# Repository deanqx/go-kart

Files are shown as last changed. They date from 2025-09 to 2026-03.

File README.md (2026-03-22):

# JCS-BK_1091_GO-KART_Blinker_Lenkrad_Anzeige

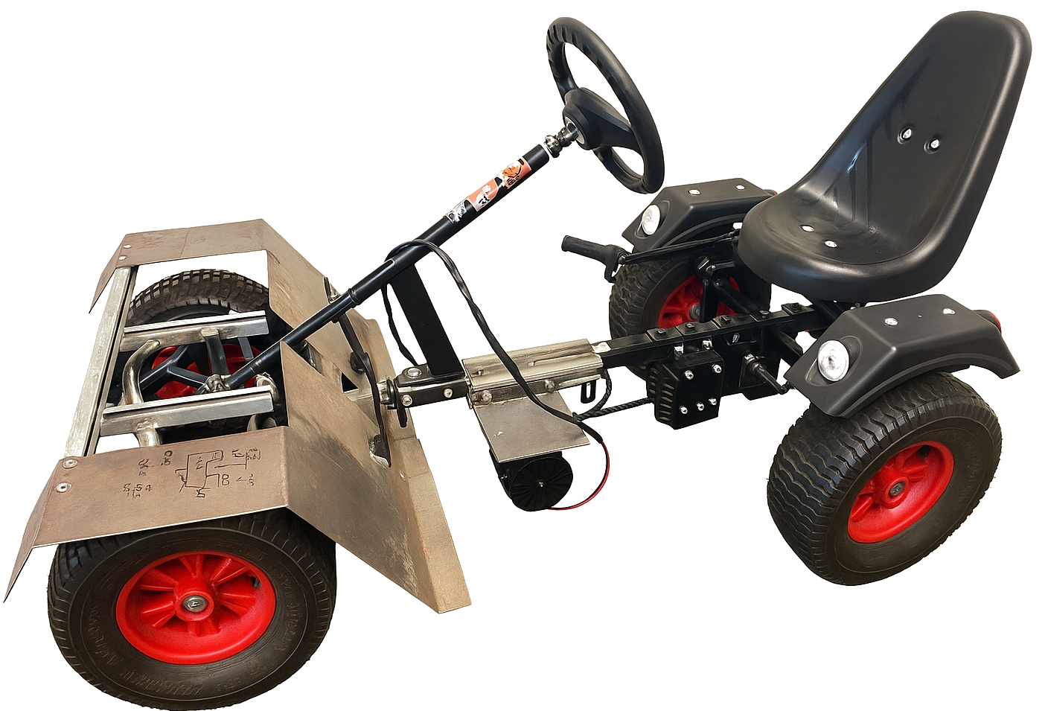
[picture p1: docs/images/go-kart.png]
Preview image of Go-Kart


Die gesamte Dokumentation befindet sich unter `docs/pdf/JCS-BK_1091_GO-KART_Blinker_Lenkrad_Anzeige_Dokumentation_DeanS.pdf` gefunden werden.

Remote repo

# Abstract

For several years, students at the technical high school have been working on upgrading a go-kart by
integrating systems typically found in modern cars. The individual modules communicate via a CAN
bus network, similar to that used in real vehicles. Two microcontrollers from the AVR family are used
throughout the system. The task is devided into multiple projects − one for each student.
This document describes the development of the light modules and the cockpit module. There is also a
video showcasing the development. The lighting system consists of four modules, one for each corner
of the vehicle. The two front modules support upper beam, lower beam, and daytime running lights,
while the two rear modules provide tail, brake, and reverse lights.
The cockpit module includes a display, a horn, and several buttons mounted on the steering wheel. It
serves as the central interface between the driver and the vehicle systems. The display presents
information such as speed, battery charge, current gear, light status, and other relevant data. Using the
steering wheel buttons and switches, the driver can control things like the driving direction, light
mode, blinker direction, horn and gear.
All required tasks of this project were successfully completed. The service provider (TIO) did not
finish the Java-based frontend; however, the serial communication interface has already been
implemented. Since the other projects have not yet integrated CAN bus communication into their
modules, communication between the cockpit and the other systems is currently not possible. In
addition, a 3D-printed case for the display and caps for the buttons could be developed in the future.

# Kurzfassung

Seit mehreren Jahren arbeiten Schüler der gymnasialen Oberstufe Bereich Technik daran, ein Go-Kart
durch die Integration von Systemen, die typischerweise in modernen Autos zu finden sind,
aufzurüsten. Die einzelnen Module kommunizieren über CAN-Bus, ähnlich wie es in echten
Fahrzeugen verwendet wird. Im gesamten System kommen zwei Mikrocontroller aus der AVR-Familie
zum Einsatz. Die Aufgabe ist in mehrere Projekte unterteilt – eines für jeden Schüler.
Dieses Dokument beschreibt die Entwicklung der Lichtanlage, des Lenkrads und der Tachoanzeige.
Des weiteren gibt es ein Video in dem die Entwicklung gezeigt wird. Die Lichtanlage besteht aus vier
Modulen, eines für jede Ecke des Fahrzeugs. Die beiden vorderen Module unterstützen Fernlicht,
Abblendlicht und Tagfahrlicht, während die beiden hinteren Module Rücklicht, Bremslicht und
Rückfahrlicht liefern.
Das Cockpitmodul umfasst ein Display, eine Hupe und mehrere am Lenkrad angebrachte Taster. Es
dient als zentrale Schnittstelle zwischen dem Fahrer und den Fahrzeugsystemen. Das Display zeigt
Informationen wie Geschwindigkeit, Batterieladestand, aktueller Gang, Lichtstatus und andere
relevante Daten an. Mit den Tasten und Schaltern am Lenkrad kann der Fahrer beispielsweise die
Fahrtrichtung, den Lichtmodus, die Blinkerrichtung, die Hupe und den Gang steuern.
Alle gegebenen Aufgaben dieses Projekts wurden erfolgreich abgeschlossen. Der Dienstleister (TIO)
hat das Java-basierte Frontend nicht fertiggestellt, jedoch wurde die serielle Schnittstelle bereits
implementiert. Da die anderen Projekte die CAN-Bus-Kommunikation noch nicht in ihre Module
integriert haben, ist eine Kommunikation zwischen dem Cockpit und den anderen Systemen derzeit
nicht möglich. Darüber hinaus könnte in Zukunft ein 3D-gedrucktes Gehäuse für das Cockpit und
Kappen für die Lenkrad-Taster entwickelt werden.

# Credits

Dieses Projekt verwendet AVR-Bibliotheken, darunter:

- Eine verbesserte Version von [dergraaf/avr-can-lib](https://github.com/dergraaf/avr-can-lib)
  welche auf den ATmega16M1 angepasst wurde.
- USART Bibliothek [jnk0le/AVR-UART-lib](https://github.com/jnk0le/AVR-UART-lib)

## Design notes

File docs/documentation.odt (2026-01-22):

BERUFLICHES GYMNASIUM
TECHNIK

JOHANN-CONRAD-SCHLAUN-BERUFSKOLLEG


Dokumentation

Go-Kart
Blinker Lenkrad Anzeige

Dean Schneider

Auftraggeber: | Michael Schmidt
Projektleitung: | Henry Otto
Projektnummer: | JCS-BK_1091_GO-KART
Jahrgang: | GYT26
Fach: | Projekt mit Elektrotechnik und Informatik
Verfasser: | Dean Schneider
E-Mail: | dschneider@schueler.jcsbk.de
Projektstart: | 1. September 2025
Projektende: | 20. März 2026
Letzte Änderung: | 22. Januar 2026

# Abstract

[englische version]

# Abstrakt

In den vergangen Jahren haben immer wieder Gruppen der gymnaliasen Oberstufe aus dem Technikbereich an dem Kettcar gearbeitet. Das Ziel ist mehrere Module eines KFZ im kleinen Aufzubauen (siehe 2.1 Team, S. 3). Dabei kommunizieren alle Module über CAN-Bus. Dies ist die Dokumentation zu dem Projekt welches die Lichtanlage, Lenkrad und die Tachoanzeige (Cockpit-Display) behandelt.

[aktueller Stand]

[was muss noch gemacht werden]

# Einleitung

Diese Dokumentation richtet sich an Personen, die dieses Projekt weiterführen oder warten möchten. Die Themen sind nach ihrer Priorität für das Nachschlagen geordnet. Das bedeutet, dass zunächst der aktuelle Aufbau (das Ergebnis) beschrieben wird, anschließend die Entwicklung hin zum aktuellen Aufbau und schließlich die Grundlagen zur Bedienung der Software.

Gesamte Anleitung für Linux um genau zu sein für die Arch Distribution.

MCU (Microcontroller Unit) entspricht Mikrocontroller

Das hier genannte Cockpit-Display wird in anderen Dokumentationen Tacho, Tachodisplay oder einfach nur Display genannt. Das OLED-Display wird Debug-Display genannt, um Verwechselung zwischen den beiden Displays zu vermeiden.

Hexadezimalzahlen werden durch 0x gekennzeichnet (z. B. 0xFF oder 0x003B).

# Ergebnis

## Team

Dieses Projekt wird in enger Zusammenarbeit mit dem Team realisiert. So muss die Kommunikation abgesprochen werden. Die Verteilung der Aufgaben sieht wie folgt aus:

Name | Aufgabe
Henry Otto | Motoransteuerung und Auslesung der Pedalen
Iuri Merklein Muniz | Elektrische Bremse und Gangschaltung
Tammo Lohe | Ladeelektronik, Batterie und Solar
Dean Schneider | Lenkrad, Cockpitdisplay und die Beleuchtung

Tabelle 1: Team

## Kommunikation zwischen den Projekten

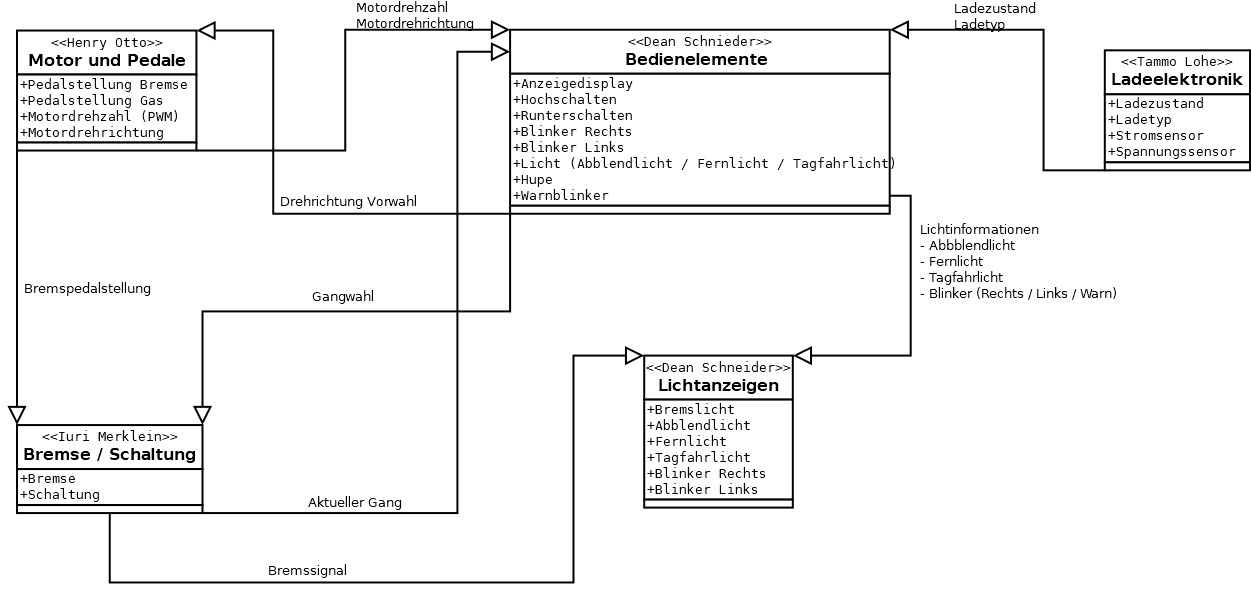
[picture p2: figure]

Abbildung 1: Kommunikationsdiagramm

## Dateistruktur

Der Quellcode und weitere Dateien des Projektes sollten von dem Projektleiter bereitgestellt werden.

├── CMakeLists.txt

├── docs

│ ├── circuit

│ │ ├── circuit.kicad_pcb

│ │ ├── circuit.kicad_prl

│ │ ├── circuit.kicad_pro

│ │ └── circuit.kicad_sch

├── libs

│ └── usart

│ ├── CMakeLists.txt

│ ├── include

│ │ ├── usart_config.h

│ │ └── usart.h

│ └── src

│ └── usart.c

├── LICENSE

├── README.md

└── src

├── cockpit_display.h

├── hal.h

└── main.c

## Mikrocontroller

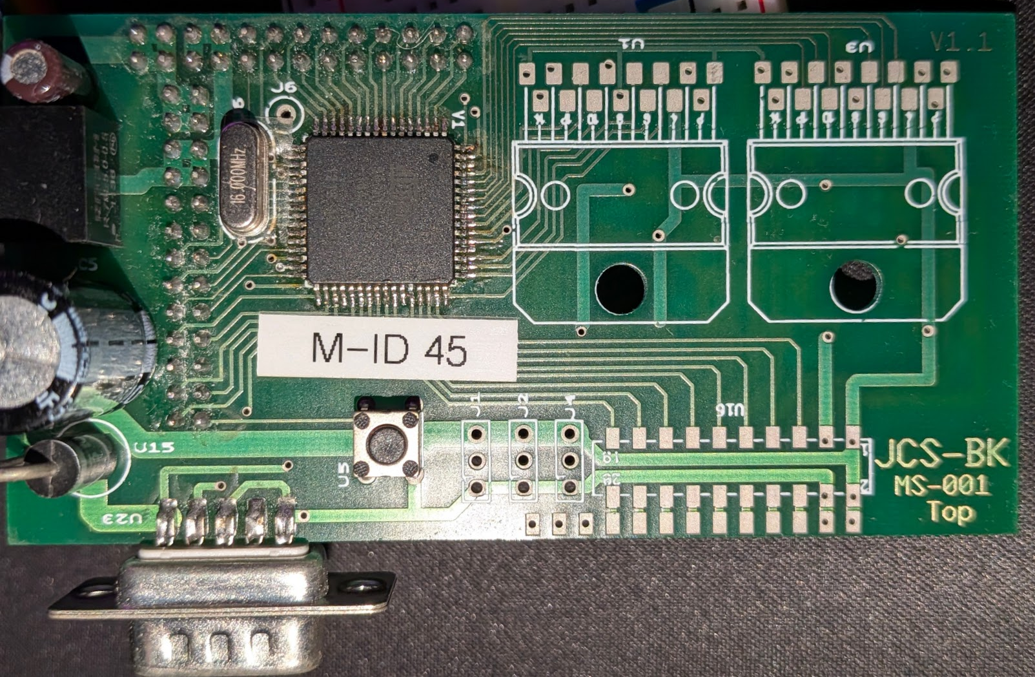
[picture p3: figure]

Abbildung 2: Masterplatine mit AT90CAN32 (MS-001)

## Cockpit-Display (Tacho)

Das Display ist von Nextion und wird mit der Nextion typischen Software programmiert/eingestellt. Auf dem Glass befindet sich ein Riss von einem Vorgänger. Christian Barth (JCS-BK_1046) hat das Display gestaltet.

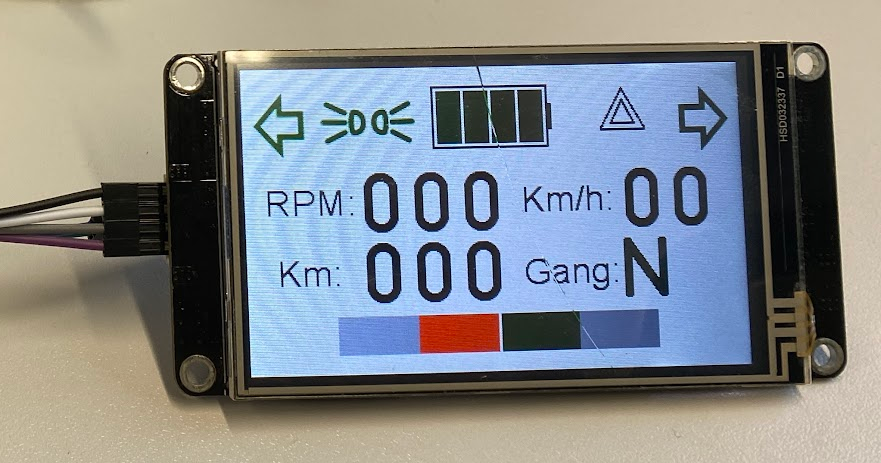
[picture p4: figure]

Abbildung 3: Cockpit-Display (NX4024K032)

[liste der befehle]

So kann man zum Beispiel mit dieser Nachricht an das Display den linken Blinker einschalten:

$ stty -F /dev/ttyUSB0 9600

$ printf 'bL.pic=1\xFF\xFF\xFF' > /dev/ttyUSB0

Erklärung dieser Befehle lässt sich unter 4.2.2 Rohdaten übertragen (siehe S. 17) finden.

## Debug-Display (OLED-Display)

Das verwendete Display ist das typische Arduino OLED-Display mit dem eingebauten SSD1306 Chip. Dieser wird über I²C angesteuert.

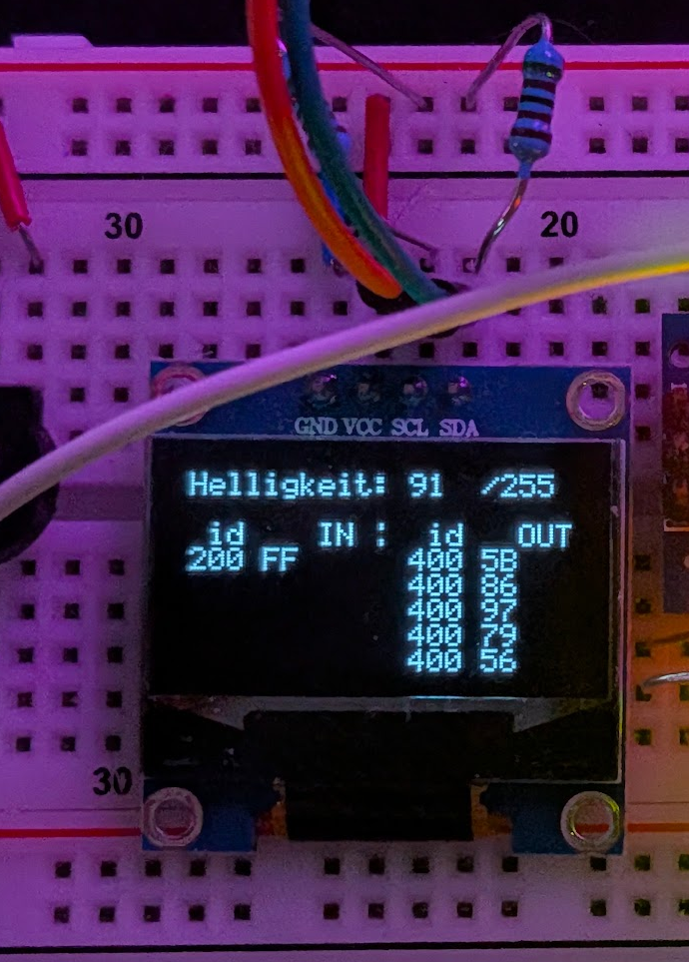
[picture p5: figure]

Abbildung 4: Debug-Display (OLED-Display mit SSD1306)

In diesem Projekt wird die Bibliothek oled-display von Sylaina (https://github.com/Sylaina/oled-display) verwendet.

## Bluetooth und UART

In diesem Projekt wird die Bibliothek AVR-UART-lib von jnk0le (https://github.com/jnk0le/AVR-UART-lib) verwendet.

Bluetooth-Name: Blinker_Anzeige

Bluetooth-Passwort: 1234

## CAN-Bus

CAN-Bus Bitrate: 125 kbits

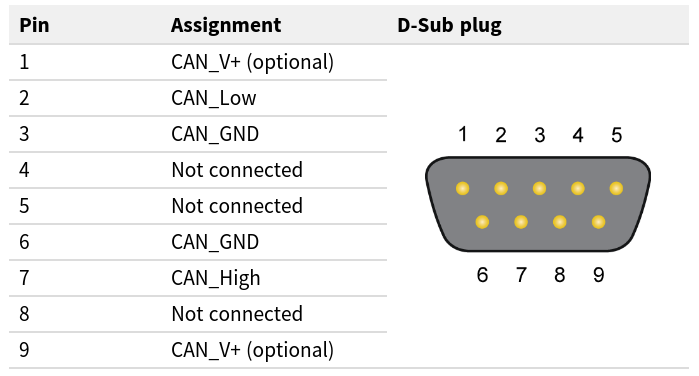
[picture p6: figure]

Abbildung 5: männlicher CAN D-Sub Anschluss nach CiA® 106 (Quelle: PCAN-USB Anleitung)

# Entwicklung

In diesem Kapitel wird der Prozess wie es Ergebnis kam dargestellt. Der aktuelle Stand des Projektes befindet sich im Kapitel 2 Ergebnis (Beginn S. 3).

## Programmierer

Ein Arduino besitzt einen Bootloader welcher den Eingang des UART in den Speicher schreibt, er programmiert sich also selbst. Allerdings besitzt der AVR MCU (AT90CAN32) von der Masterplatine keinen Bootloader, er wird über ISP (In-System Programming) programmiert.

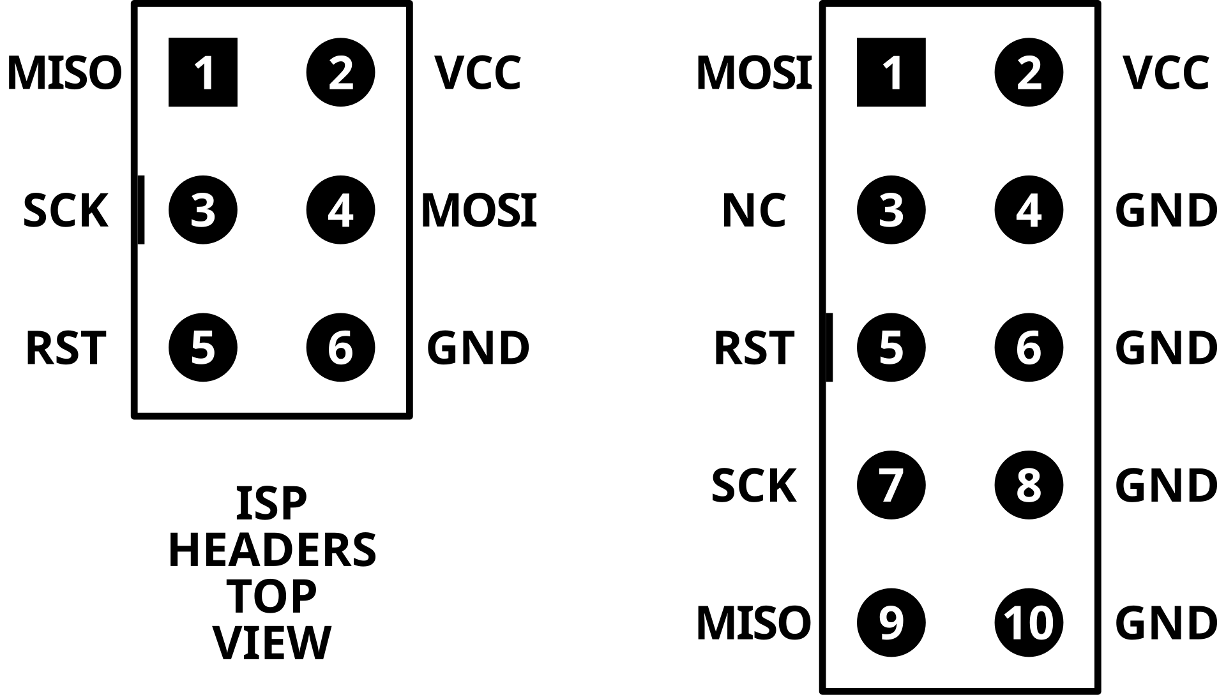
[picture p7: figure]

Abbildung 6: ISP Pinbelegung (Quelle: wikipedia.org)

Beim Kauf eines Programmierers ist darauf zu achten, dass er eine Open-Source Firmware hat, zum Beispiel USBasp.

Falls man nicht weiß welche Programmierer-Firmware man hat, kann man diese über die ID herausfinden:

$ lsusb

Zum Hochladen wird avrdude verwendet dasselbe Tool wie Microchip Studio verwendet. Als Erstes muss avrdude installiert werden. Zum Beispiel auf Arch mit:

$ sudo pacman -S avrdude

Anschließend kann man sich mit diesem Befehl alle voreingestellte Programmierer-Konfigurationen ausgeben lassen:

$ avrdude -c ?

## Masterplatine mit dem AT90CAN32

Das Projekt JCS-BK MS-001 enthält Schaltpläne zur AT90CAN32 Masterplatine. Pläne zur Addon-Platine, dass heißt dort wo die serielle und ISP Verbindung angeschlossen wird, lassen sich unter JCS-BK MS-003 finden.

### Erste Schritte

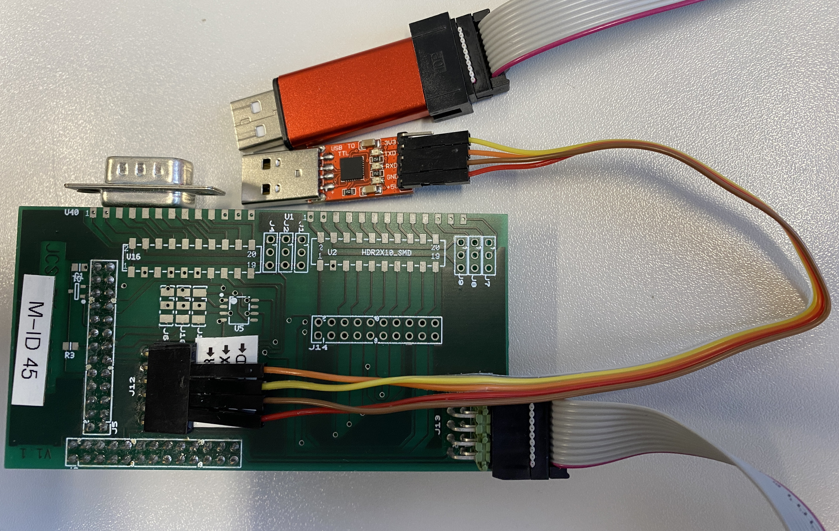
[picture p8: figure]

Abbildung 7: Masterplatine mit serieller und ISP Verbindung

Bevor man komplexe Programme programmiert sollte man erstmal die Programmier-Schnittstelle überprüfen. In diesem Beispiel wird TX zwischen High und Low gewechselt. Mein USB-zu-Seriell Gerät hat eine LED für RX, darüber kann ich den Spannungswechsel sehen. Kurz gesagt wird eine blinkende LED zum Feststellen der Funktion verwendet.

Warnung: In Abbildung 7 ist der Aufbau zu sehen. Es ist wichtig zu überprüfen ob der Programmierer eine Spannung liefert (z. B. 5V), denn dann sollte die Spannungsversorgung des USB-zu-Seriell Adapters von der Masterplatine getrennt werden. Oft ist dies nicht nötig, es reduziert jedoch das Risiko eines Schadens durch Ausgleich-Ströme.

Hier ist der Code zum Blinken lassen der RX LED (siehe 4.1 Kompilieren und Hochladen, S. 16):

#include <avr/io.h>

#include <util/delay.h>

static const uint8_t TXD1 = PD3;

int main(void) {

DDRD = 1 << TXD1;

while (1) {

PORTD ^= 1 << TXD1;

_delay_ms(500);

}

return 0;

}

## Cockpit Display (Tacho)

### Erstes Display

Eigentlich sollte das NX8048K070_011C Display von Nextion verwendet verwenden. Allerdings war ich direkt zu Beginn des Projektes unaufmerksam und habe ausversehen an das 5V Display 14V angeschlossen, das Display leuchtete bis die Spannungsversorgung entfernt wurde. Der Spannungsregler des Displays ist beschädigt und eventuell auch weitere Bauteile. Diese müssten ausgetauscht werden, wobei sich die Frage stellt ob sich der Zeitaufwand lohnt, insbesondere da es sich um SMD Bauteile handelt und man nicht eindeutig die Bauteilbezeichnung lesen kann.

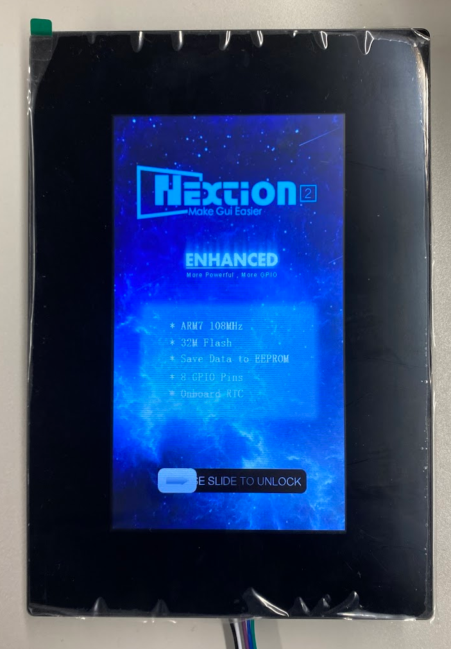
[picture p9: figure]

Abbildung 8: Nextion Display (NX8048K070_011C)

Nun muss das vorherige Display, welches allerdings von JCS-BK_1046 bereits gestaltet und eingestellt wurde, verwendet werden.

Abbildung 9: Ersatz Bauteil suche für Spannungsregler (https://smd.yooneed.one)

## Bluetooth-Modul

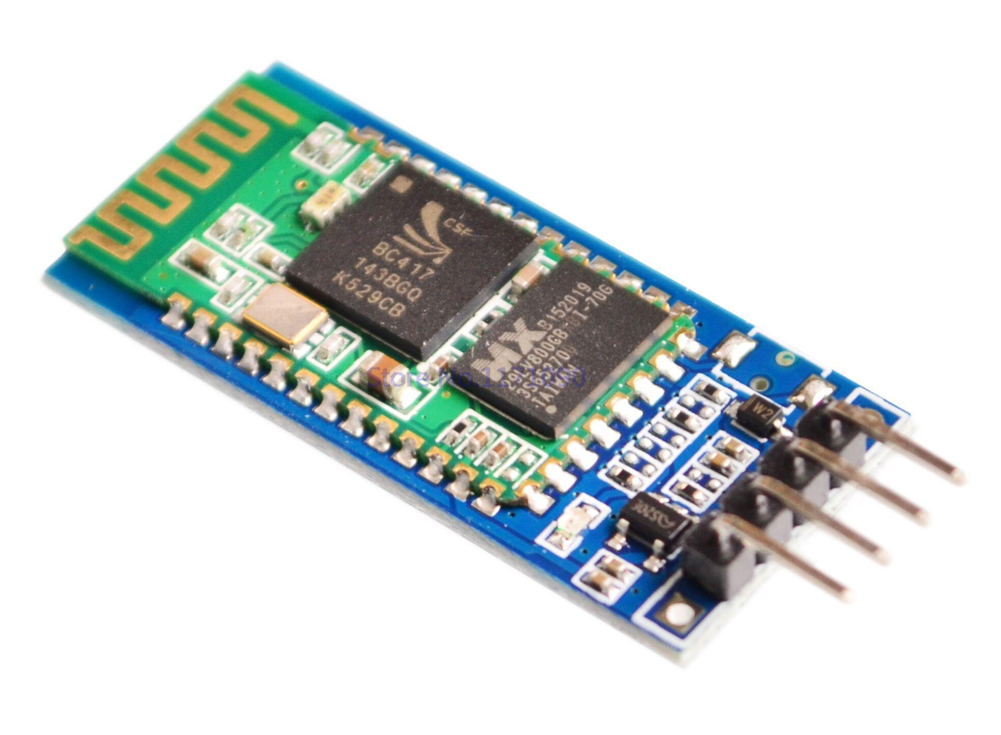
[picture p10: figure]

Abbildung 10: Bluetooth-Modul mit HC-06 Oberseite (Quelle: roboter-bausatz.de)

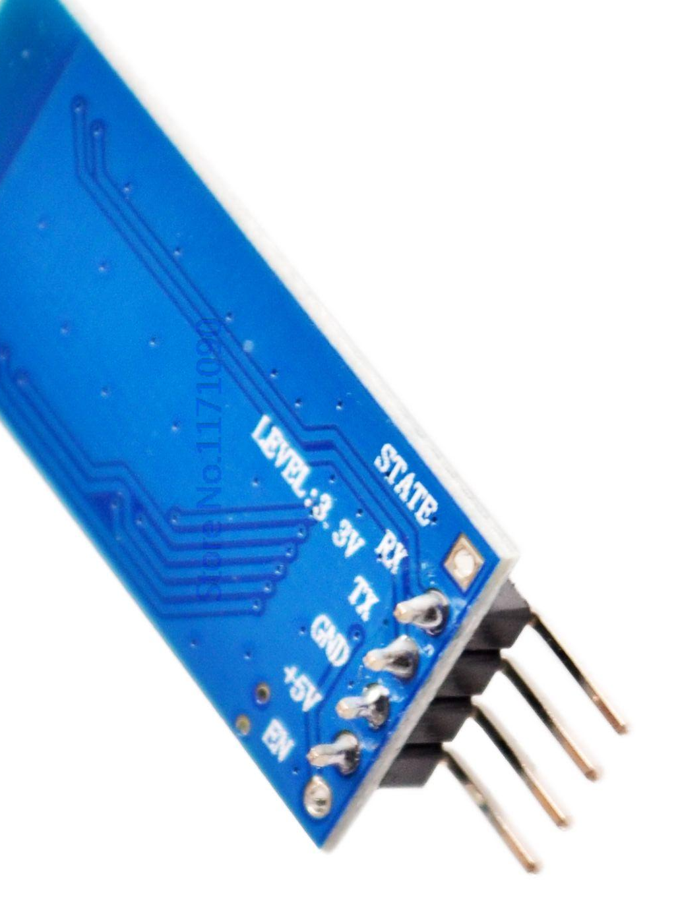
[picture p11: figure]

Abbildung 11: Bluetooth-Modul mit HC-06 Unterseite
(Quelle: roboter-bausatz.de)

In Abbildung 10 ist das verwendete Bluetooth-Modul zu sehen. Bei der grünen aufgelöteten Platine handelt es sich um den HC-06 mit dem CSR BC417BQN (Bluetooth Chip). Der HC-06 unterscheidet sich vom HC-05, indem er nur als Slave fungieren kann. Das bedeutet der HC-06 kann nicht ein Gerät (z. B. Laptop) suchen und sich mit ihm Verbinden. Zu erkennen ist der HC-06 daran, dass nur 4 Pins herausgeführt sind.

Die Pins TX und RX fungieren als UART Schnittstelle.

PIN | Beschreibung
RX (3,3V) | Receive – Eingang UART des Moduls, benötigt einen Spannungsteiler
TX | Transmit – Ausgang UART des Moduls
GND | Verbindung zu GND
5V | +5V Versorgungsspannung

### Test und konfigurieren mit USB-zu-Seriell-Konverter

Das Bluetooth-Modul wird mit dem USB-zu-Seriell-Konverter verbunden. Es sind keine Widerstände nötig da der Konverter mit 3,3 V arbeitet.

Bluetooth-Modul | USB-zu-Seriell-Konverter
RX | TX
TX | RX
GND | GND
5V | +5V

Die LED des Bluetooth-Moduls sollte blinken, sobald die Spannungsversorgung hergestellt wurde. Dies bedeutet das auf Verbindung gewartet wird.

Nun können die Befehle zum Konfigurieren über UART (siehe 4.2 UART Übertragung, S. 17) mit einer Baud-Rate von 9600 bps übertragen werden. Beim HC-06 kann kein „AT Command Mode“ aktiviert werden. Er befindet sich immer im Kommando-Modus, wenn keine Verbindung besteht was an dem Blinken der LED zu erkennen ist.

Befehl senden | Beispiel | Rückgabe vom Modul
AT | | OK
AT+VERSION | | OKlinvorV1.8
AT+NAME<Name> | AT+NAMEBlinker_Anzeige | OKsetname
AT+PIN<PIN> | AT+PIN1234 | OKsetPIN

Es gibt weitere Befehle (siehe Datenblatt). So ist es zum Beispiel möglich die BAUD-Rate zu verändern, allerdings reicht 9600 bps völlig für den UART gebrauch aus und eine Änderung kann Projekt verwirren.

Schließlich kann man sich mit einem anderen Computer über Bluetooth Verbinden und seriell Daten an den Computer mit der UART Verbindung senden (siehe 4.3 Bluetooth Übertragung, S. 19).

### Schaltung mit Mikrocontroller

Der TX Pin des Bluetooth-Moduls wird über eine Diode geleitet, da der MCU noch nicht initialisiert sein könnte und damit der RX des MCU High ist und TX Low, dadurch entsteht ein Kurzschluss. Der TX Pin des MCU wird über einen Spannungsteiler angeschlossen da der MCU mit 5V und das Modul mit 3.3 V arbeitet. Im Folgenden wird der Spannungsteiler dimensioniert.

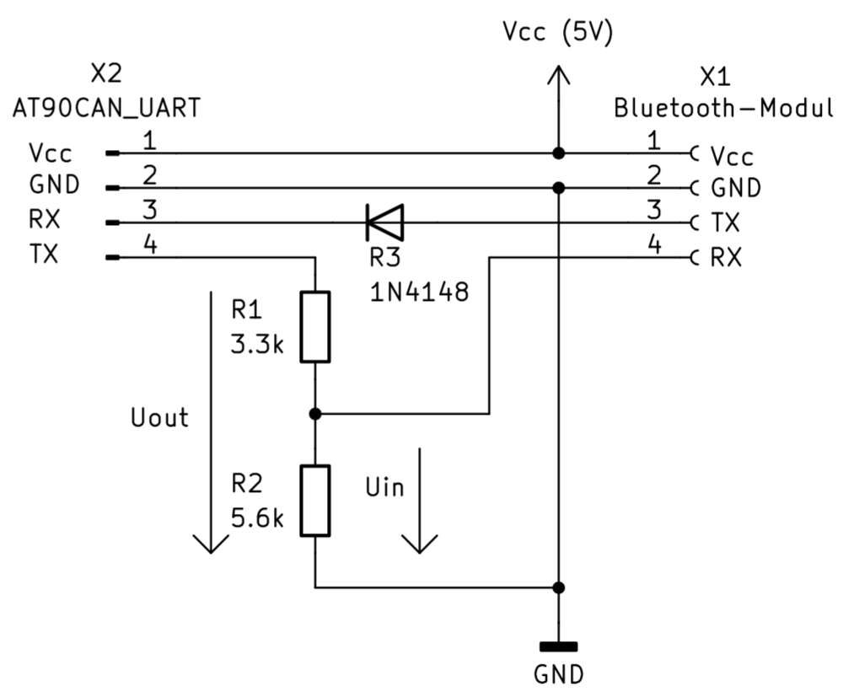
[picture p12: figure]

Schaltplanausschnitt 1: Anschluss des Bluetooth-Modul an die Masterplatine

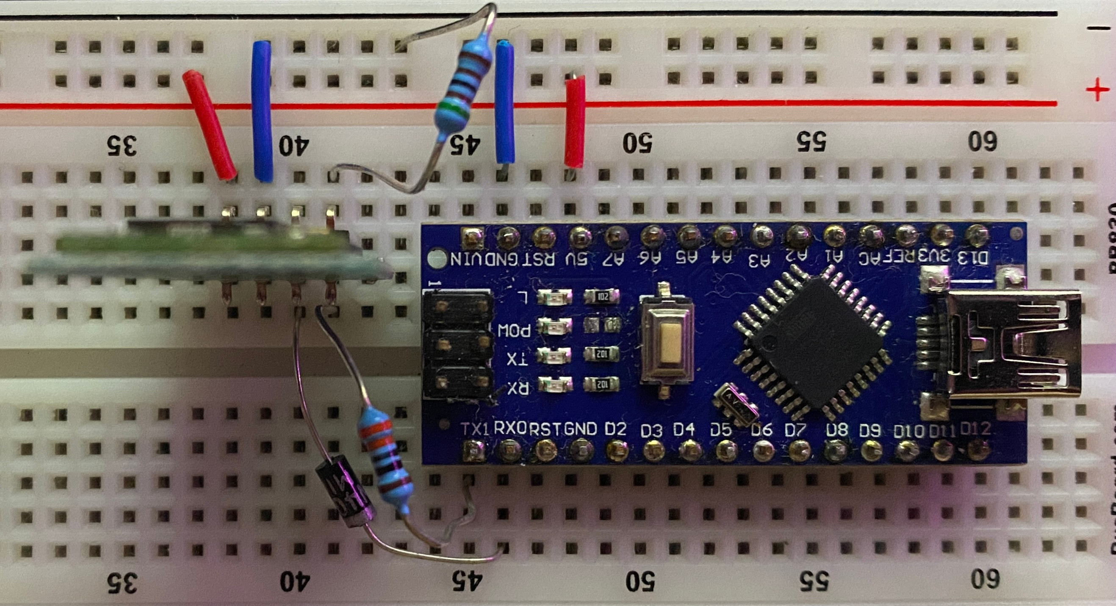
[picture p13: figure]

Abbildung 12: Bluetooth-Modul Schaltung mit Arduino

Die Eingangsspannungen beziehen sich auf den CSR BC417BQN.

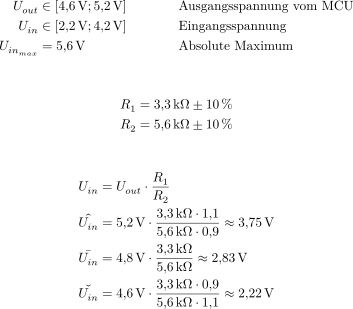
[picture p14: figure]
TexMaths 12§latex§\begin{align*} U_{out} &\in [\SI{4.6}{\volt}; \SI{5.2}{\volt}] &&\text{Ausgangsspannung vom MCU}\\ U_{in} &\in [\SI{2.2}{\volt}; \SI{4.2}{\volt}] &&\text{Eingangsspannung}\\ U_{in_{max}} &= \SI{5.6}{\volt} &&\text{Absolute Maximum} \end{align} \begin{align*} R_1 &= \SI{3.3}{\kilo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

Schließlich kann man die UART-Ausgabe über Bluetooth auslesen und Daten an den MCU über UART senden (siehe 4.3 Bluetooth Übertragung, S. 19).

Warnung: Hochladen über den Bootloader wird nicht funktionieren da ein Reset benötigt wird.

# Grundlagen

In diesem Kapitel werden die Grundlagen zur bedienung der Software erklärt. So das man dieses Projekt weiter entwickeln oder warten kann. Dabei richtet sich diese Anleitung an Linux-Nutzer, einige Programme sind ebenfalls für andere System wie Windows verfügbar.

## Kompilieren und Hochladen

Benötigtes Paket:

- cmake

CMake und Make sind Werkzeuge, die den Bau von Programmen steuern, ähnlich wie eine IDE (Microchip Studio), nur über die Kommandozeile. CMake erzeugt Baupläne, die das System und den Compiler kennen, und Make führt diese Pläne aus, übersetzt den Code und erstellt die ausführbaren Dateien.

$ cmake -B build

Dieser Befehl erzeugt in einem neuen Verzeichnis namens „build“ alle notwendigen Dateien, die für den Bau des Projekts benötigt werden. CMake liest die „CMakeLists.txt“ Datei aus dem „src“ Verzeichnis, plant welche Dateien kompiliert werden müssen, und erstellt die Bauanweisungen (Makefile).

$ make

Make liest die von CMake erzeugten Makefiles und führt die Anweisungen aus. Es kompiliert die Quellcodes in Maschinencode und erstellt daraus die fertigen Programme oder Bibliotheken. Make sorgt dafür, dass nur die geänderten Dateien neu gebaut werden, was Zeit spart.

## UART Übertragung

### Text übertragen

Benötigtes Paket:

- minicom

1. USB-zu-Seriell-Konverter Geräte Schnittstelle finden (z. B. /dev/ttyUSB0 oder /dev/ttyACM0):

$ ls /dev/tty*

2. Serielle Übertragung öffnen. In diesem Fall mit dem Tool „minicom“ und eine BAUD-Rate von 9600 bps:

$ minicom -D /dev/ttyUSB0 -b 9600

### Rohdaten übertragen

Um Binär oder Hexadezimal über UART zu senden kann man nicht minicom verwenden. In diesem Beispiel wird das Standard-Linux-Interface genutzt.

1. BAUD-Rate einstellen (z. B. 9600 bps):

$ stty -F /dev/ttyUSB0 9600

2. Nachricht senden (z. B. für das Cockpit-Display):

$ printf 'bL.pic=1\xFF\xFF\xFF' > /dev/ttyUSB0

Hierbei ist die Nachricht: „bL.pic=1“ und drei mal 0xFF.

### CAN Sniffing (PCAN-USB)

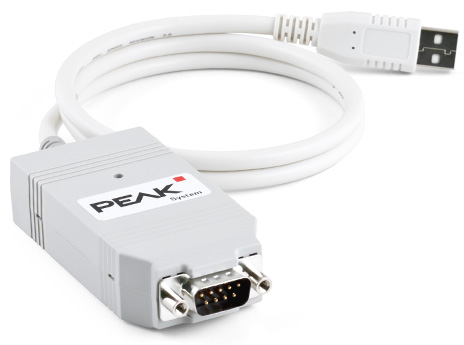
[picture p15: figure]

Abbildung 13: PCAN-USB (Quelle: peak-system.com)

Benötigte Pakete:

- can-utils

Als CAN-Interface für USB wird der PCAN-USB IPEH-002021 von PEAK-System verwendet.

Der D-Sub stecker von allen Modulen ist nach CiA® 106 (siehe Abbildung 5: männlicher CAN D-Sub Anschluss nach CiA® 106 (Quelle: PCAN-USB Anleitung), S. 8)

#### Empfangen

Der folgende Befehl aktiviert das Netzwerk-Interface can0 als CAN-Bus-Schnittstelle und setzt dabei die Übertragungsrate auf 125 kbit/s. Dieser Schritt muss nur einmal durchgeführt werden.

$ sudo ip link set can0 up type can bitrate 125000

Anschließend können Nachrichten des CAN-Busses augegeben werden.

$ candump can0

Mögliche Ausgabe:

can0 400 [8] 01 02 02 03 04 05 06 07

#### Senden

Beispiel mit ID = 0x4AA und erstes Datenbyte = 0x0F, zweites Datenbyte = 0x55:

$ cansend 4AA#0F55

#### Fehlerbehebung

Eventuell muss der Treiber von PEAK-System manuell installiert werden.

Ob ein Treiber installiert ist kann man zum Beispiel über die System-Logs herausfinden. Da der Treiber jenach Distrobution auch anders als peak_usb benannt sein kann, muss man eventuell den gesuchten Eintrag mit can0, pcan oder peak suchen.

$ sudo dmesg | grep -i peak_usb

Wenn die Ausgabe so ähnlich aussieht ist der Treiber installiert:

peak_usb 3-2:1.0: PEAK-System PCAN-USB adapter hwrev 28 serial

peak_usb 3-2:1.0 can0: attached to PCAN-USB channel 0

usbcore: registered new interface driver peak_usb

Falls der Treiber nicht installiert ist kann man ihn über den Package-Manager des Systems herunterladen oder über die Webseite von PEAK-Systems.

## Bluetooth Übertragung

In diesem Kapitel wird erklärt wie man eine Verbindung mit dem Bluetooth-Modul (siehe 3.4 Bluetooth-Modul, S. 12) aufnehmen kann.

Warnung: IOS unterstützt keine Verbindung zu SPP (Serial Port Profile), sondern nur BLE (Bluetooth Low Energy). Da es sich hier um SPP handelt, ist keine Verbindung mit dem iPhone oder iPad möglich.

Benötigte Pakete:

- minicom
- bluez
- bluez-deprecated-tools

Die Arch Wiki hat eine ausführliche Erklärung wie man sich mit einem Bluetooth-Gerät verbindet (siehe https://wiki.archlinux.org/title/Bluetooth).

Nachdem eine Bluetooth-Verbindung hergestellt wurde, muss sie einer device-Datei gebunden werden:

$ sudo rfcomm bind rfcomm0 <MAC Addresse des Bluetooth-Moduls>

Anschließend kann eine serielle Übertragung (siehe 4.2 UART Übertragung, S. 17) mit einer BAUD-Rate von 9600 bps hergestellt werden:

$ minicom -D /dev/rfcomm0 -b 9600

Das Blinken auf dem Bluetooth-Modul sollte aufhören und die Status-LED sollte konstant Leuchten.

# Eidesstattliche Erklärung

Hiermit versichere ich, dass ich die vorliegende Dokumentation selbstständig verfasst und keine anderen als die angegebenen Quellen und Hilfsmittel benutzt habe. Alle Stellen, die wörtlich oder sinngemäß aus veröffentlichten oder nicht veröffentlichten Schriften entnommen wurden, sind als solche kenntlich gemacht.

Ferner versichere ich, dass die vorliegende Arbeit noch nicht in einem anderen Prüfungsverfahren vorgelegen hat.

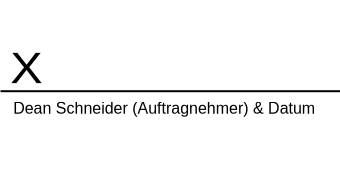
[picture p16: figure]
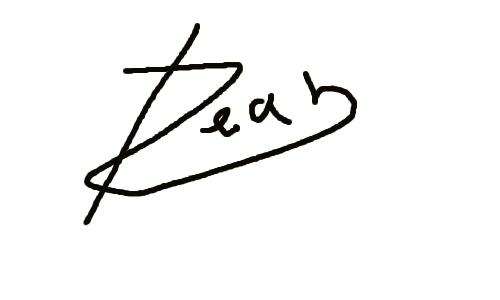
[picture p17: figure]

# Anhang

## Projekte der Vorgänger

Hiervon sind hauptsächlich JCS-BK_1025 (Schaltpläne für Lichtanlage), JCS-BK_1049 (Lichtanlage) und JCS-BK_1046 (Lenkradknöpfe, Cockpitdisplay) von Bedeutung.

Tabelle 2: alte Projekte

## Tagesziele

Tabelle 3: Tagesziele

## Meilensteine

Start- datum | Ziel- datum | Zeit(h) | Thema (Aufgabe)
01.09.25 | 11.09.25 | | Festlegen des Themas und der Projektteams (Informationssammlung, Pflichtenheft zur Aufgabenfixierung, Aufgabenverteilung im Team und Anfertigung des Detailterminplans)
12.09.25 | 08.10.25 | 18 | Abgabe des Pflichtenhefts
08.10.25 | 30.11.25 | 34 | Schaltplanerstellung / Programmierung von Modulen / Testaufbau / Modultests
08.10.25 | 30.11.25 | 5 | Abgabe der Draft 1 - Dokumentationsentwurf
| | | Statusermittlung / Terminplanprüfung
| | | Schaltplan- und Layouterstellung / Programmierung von Modulen Testaufbau / Modultests / Dokumentation
| | | Programmtests, Dokumentation, Fehleranalyse, Fehlerbeseitigung
| | | Abgabe der Draft2-Dokumentation 7:35 keine Verlängerung
| | | Programmtests, Dokumentation, Fehleranalyse, Fehlerbeseitigung
| | | Präsentation des Projekts Weiterentwicklung
| | | Präsentation der Ergebnisse als Impress-Vortrag
| | | Präsentation der Zwischenstände am Tag der offenen Tür
| | | Abgabe des Projekts mit Abschluss-Dokumentation 24:00
| | | Leistungsüberprüfung / Produktabnahme

## Terminplan

Tabelle 4: Terminplan 01.09. - 19.09.2025

Tabelle 5: Terminplan 20.10. - 07.12.2025

Tabelle 6: Terminplan 08.12.2025 - 25.01.2026

Tabelle 7: Terminplan 26.01. - 15.03.2026

Tabelle 8: Terminplan 16.03. - 10.05.2026

## Abbildungsverzeichnis

Abbildung 1: Kommunikationsdiagramm 3

Abbildung 2: männlicher CAN D-Sub Anschluss nach CiA® 106 (Quelle: PCAN-USB Anleitung) 5

Abbildung 3: ISP Pinbelegung (Quelle: wikipedia.org) 6

Abbildung 4: Masterplatine mit serieller und ISP Verbindung 7

Abbildung 5: (https://smd.yooneed.one) 8

Abbildung 6: Bluetooth-Modul mit HC-06 Oberseite (Quelle: roboter-bausatz.de) 9

Abbildung 7: Bluetooth-Modul mit HC-06 Unterseite (Quelle: roboter-bausatz.de) 9

Abbildung 8: Bluetooth-Modul Schaltung mit Arduino 11

Abbildung 9: PCAN-USB (Quelle: peak-system.com) 14

## Schaltplanausschnitte

Schaltplanausschnitt 1: Anschluss des Bluetooth-Modul an die Masterplatine 11

## Tabellenverzeichnis

Tabelle 1: Team 3

Tabelle 2: alte Projekte 17

Tabelle 3: Tagesziele 18

Tabelle 4: Terminplan 01.09. - 19.09.2025 20

Tabelle 5: Terminplan 20.10. - 07.12.2025 21

Tabelle 6: Terminplan 08.12.2025 - 25.01.2026 22

Tabelle 7: Terminplan 26.01. - 15.03.2026 23

Tabelle 8: Terminplan 16.03. - 10.05.2026 24

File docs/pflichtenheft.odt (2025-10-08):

BERUFLICHES GYMNASIUM
TECHNIK

JOHANN-CONRAD-SCHLAUN-BERUFSKOLLEG


Pflichtenheft

Go-Kart
Blinker Lenkrad Anzeige

Dean Schneider

Auftraggeber: | Michael Schmidt
Projektleitung: | Henry Otto
Projektnummer: | JCS-BK_1091_GO-KART
Jahrgang: | GYT26
Fach: | Projekt mit Elektrotechnik und Informatik
Verfasser: | Dean Schneider
E-Mail: | dschneider@schueler.jcsbk.de
Projektstart: | 1. September 2025
Projektende: | 20. März 2026
Letzte Änderung: | 8. Oktober 2025

# Einleitung

Dieses Dokument beschreibt wie die im Lastenheft festgelegten Anforderungen umgesetzt werden.

## Team

Dieses Projekt wird in enger Zusammenarbeit mit dem Team realisiert. So muss die Kommunikation abgesprochen werden. Die Verteilung der Aufgaben sieht wie folgt aus:

Name | Aufgabe
Henry Otto | Motoransteuerung und Auslesung der Pedalen
Iuri Merklein Muniz | Elektrische Bremse und Gangschaltung
Tammo Lohe | Ladeelektronik, Batterie und Solar
Dean Schneider | Lenkrad, Cockpitdisplay und die Beleuchtung

Tabelle 1: Team

## Kommunikation zwischen den Projekten

# Aufgabenstellung


Abbildung 1: Kommunikationsdiagramm

Entwicklung und Realisierung eines fahrzeuggestützten Armaturenbretts (Cockpitdisplay) auf Basis eines Mikrocontrollers mit Anzeige- und Bedienelementen, CAN-Bus-Anbindung, Test-Schnittstellen (Bluetooth/USB) und begleitender Dokumentation. Die Auswertungssoftware liefert die TIO.

## Hardwareanforderungen

Die folgende Aufzählung enthält Produkte von vorherigen Projekten. Falls diese nicht mehr vorhanden oder funktional sind, müssen diese dementsprechend ersetzt werden. Gegebenenfalls müssen Bauteile bestellt werden.

### Steuerung mit Mikrocontroller

Jedes Element des Go-Karts (z. B. Blinker oder Cockpitdisplay) besitzt einen eigenen Mikrocontroller. Die Mikrocontroller sind über einen CAN-Bus verbunden. Zum Einsatz kommt der ATmega16M1, der über einen integrierten CAN-Controller sowie eine UART-Schnittstelle verfügt. Voraussichtlich werden zwei UART-Schnittstellen benötigt. Die zweite Schnittstelle wird dabei softwareseitig über eine Bibliothek realisiert. Die Leiterplatte, auf der der ATmega16M1 montiert ist, wird als Masterplatine bezeichnet.

Eventuell wird der ATmega16M1 durch den stärkeren AT90CAN32 Mikrocontroller ausgetauscht. Die wichtigsten Vorteile für dieses Projekt sind unter anderem:

- zwei USART-Schnittstellen gegenüber einer beim ATmega16M1
- stärkerer CAN-Controller mit mehr Funktionen und Message Objects:
  - AT90CAN32: 15 Full Message Objects
  - ATmega16M1: 6 Message Objects
- Hardware I²C-Controller

### Beleuchtung

Front- und Rückleuchten wurden im Vorgängerprojekt erstellt (siehe 3.1.3 JCS-BK_1071_GO-KART Blinker_Lenkrad_Anzeige, S. 8).

### Lenkrad mit Steuerknöpfen

Folgende Bedienelemente sind am Lenkrad vorgesehen:

- Hochschalten
- Blinker links
- Licht (Aus / Tagfahrlicht / Fernlicht)
- Hupe
- Blinker rechts
- Herunterschalten

### Cockpitdisplay

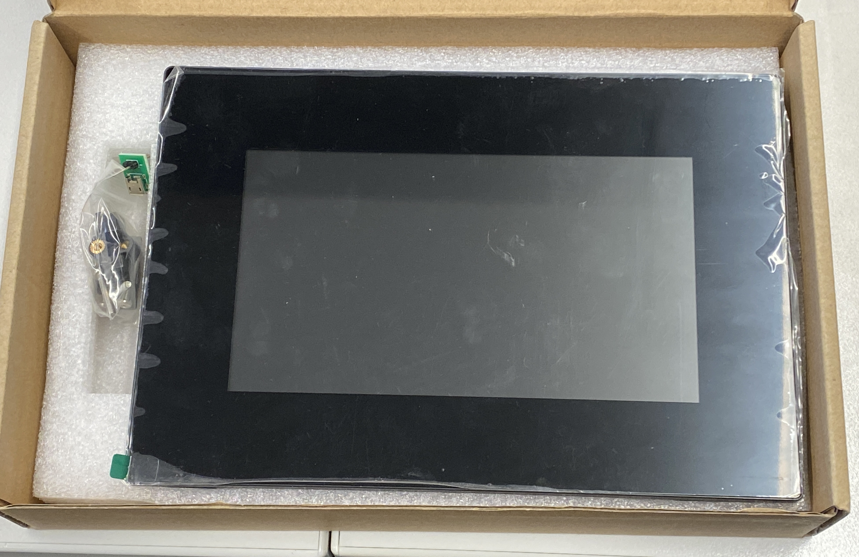
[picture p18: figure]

Abbildung 2: Display (Nextion NX8048K070)

In Abbildung 2 sieht man das Display, welches auf dem Fahrzeugarmaturenbrett befestigt wird. Das eingesetzte Display inklusive Gehäuse wird als Cockpitdisplay bezeichnet.

Das Display muss mindestens folgende Statusanzeigen darstellen: Geschwindigkeit, Batteriestatus, Gangstellung, Blinkerstatus, Fernlicht, Tagfahrlicht, Bremslicht

## Datenaustausch

### Primäre Busschnittstelle

CAN-Bus wird zum Austausch von Sensordaten und Steuerbefehlen für Systeme innerhalb des Fahrzeugs verwendet.

### Auswertungsprogramm

Ein Auswertungsprogramm, basierend auf Java, wird von der TIO erstellt. Aufbau der grafischen Benutzeroberfläche und die projektspezifische Schnittstelle sind in Abstimmung mit der TIO und dem Auftraggeber festzulegen.

### Diagnoseschnittstellen

Für jede Masterplatine stehen Bluetooth- und USB-Schnittstellen zur Verfügung. Diese ermöglichen die Kommunikation zwischen einer Masterplatine und einem Computer, auf dem die Auswertungssoftware ausgeführt wird. Die Kommunikation zwischen den Masterplatinen erfolgt ausschließlich über den CAN-Bus.

## Programmierung

Folgende Spezifikationen betreffen nur die Mikrocontroller-Programmierung und nicht das Auswertungsprogramm. Als Programmiersprache wird C eingesetzt. Programmablaufpläne werden für eine Gesamtübersicht des Programms erstellt, sie stellen den gesamten Programmablauf dar und nicht unbedingt die interne Logik. Vom Quellcode und von der Dokumentation werden regelmäßig Backups angefertigt.

### Build-Tool

Als Build-Tool wird CMake verwendet. Es wird zum Kompilieren und Hochladen der C-Dateien verwendet. Es übernimmt den Job von Atmel/Microchip Studio und ist dabei nicht an eine IDE gebunden. Außerdem ist CMake für alle Betriebssysteme (Windows, Mac und Linux) verfügbar. Alle nötigen Einstellungen können in einfachen Textdateien (CMakeLists.txt) festgelegt werden. Für AVR-Projekte nutzt man dann die Toolchain avr-gcc sowie Tools wie avr-objcopy und avrdude zum Hochladen über die serielle Schnittstelle.

Für dieses Programm wird eine genauere Erklärung erstellt.

### Code Konventionen

- Einheitliche Einrückung mit 4 Leerzeichen (keine Tabs)
- Maximale Zeilenlänge von 80 Zeichen
- Variablen und Funktionen: snake_case
- Konstanten: UPPER_CASE
- Aussagekräftige Namen statt Abkürzungen (calculate_total statt calc)
- Kommentare richten sich nach dem Google Style C++ Guide (https://google.github.io/styleguide/cppguifde.html#Comments)

## Dokumentation

### Office-Software

Als Office-Software wird LibreOffice verwendet. LibreOffice ist ein kostenloses und leistungsfähiges Office-Paket, das eine Vielzahl von Programmen für unterschiedliche Anwendungsbereiche bietet. Calc ist das Tabellenkalkulationsprogramm, mit dem man Daten berechnen, auswerten und in Diagrammen darstellen kann. Writer ist das Textverarbeitungsprogramm, das sich für das Schreiben und Formatieren von Dokumenten wie Briefe, Berichte oder wissenschaftliche Arbeiten eignet. Draw ist das Grafik- und Zeichenprogramm, mit dem man Diagramme, Skizzen, Flusspläne oder auch komplexe Illustrationen erstellen kann.

### Projekt-Dokumentation

Die Projekt-Dokumentation hält sich an die Stilvorgaben (definiert unter „Inhalt und Aufbau der Dokumenation“ im Lastenheft). Die Projekt-Dokumenation wird in LibreOffice Writer geschrieben und wird als PDF exportiert. Sie richtet sich an jemanden, welcher nichts über das Go-Kart weiß. Es wird vorausgesetzt das der Leser alles aus der Unter- und Mittelstufe des Technischen Gymnasium weiß. Die Dokumentation beinhaltet alle Informationen, um diese Aufgabenstellung fortzuführen.

### Plakat für den Tag der offenen Tür

Das Plakat stellt dieses Projekt visuell dar.

### Projektvideo

Wichte Ereignisse werden auf Video festgehalten und am Ende wird ein Zusammenschnitt erstellt, welche das Projekt visuell dokumentieren.

### Abschlusspräsentation

Zum Schluss wird eine Präsentation mit LibreOffice Impress erstellt, welche das Projekt in 15 bis 20 Minuten zusammen fasst.

## 3D-Druck

Eventuell müssen für das Display und das Lenkrad Teile aus Plastik mit dem 3D-Drucker der Schule gedruckt werden. Als CAD-Software wird FreeCAD verwendet.

## Erstellung von Platinen

Eventuell müssen Platinen gefertigt werden. Die Platinenlayouts werden mit KiCad erstellt und in das benötigte Format exportiert. Die Leiterbahnen werden nach den Vorgaben des Fräsers erstellt.

KiCad ist ein kostenloses und plattformübergreifendes EDA-Programm, das wie Multisim für das Entwerfen von Schaltplänen und Leiterplatten verwendet wird. Im Gegensatz zu Multisim ist es vollständig Open Source, läuft stabil unter Linux und wird kontinuierlich weiterentwickelt. Viele Nutzer bevorzugen KiCad, weil es weniger Fehler aufweist, professionell nutzbar ist und keine Lizenzkosten verursacht.

# Projekte der Vorgänger

Tabelle 2: alte Projekte

## Analyse des Bestehenden

Es ist davon auszugehen das die Bauteile aus den Vorgängerprojekten nicht funktionsfähig sind. Sie müssen dementsprechend ersetzt werden.

### JCS-BK_1046_GO-KART Fahrzeugarmaturenbrett

Aus der Dokumenation geht nicht hervor welche Funktion diese Bauteile erfüllen. Da der Auftrag dieses Projektes das Fahrzeugarmaturenbrett ist, kann man davon ausgehen das, das die Taster zum Steuern der Beleuchtung genutzt wird. Wie brauchbar diese Bauteile sind muss nochmal genauer untersucht werden.

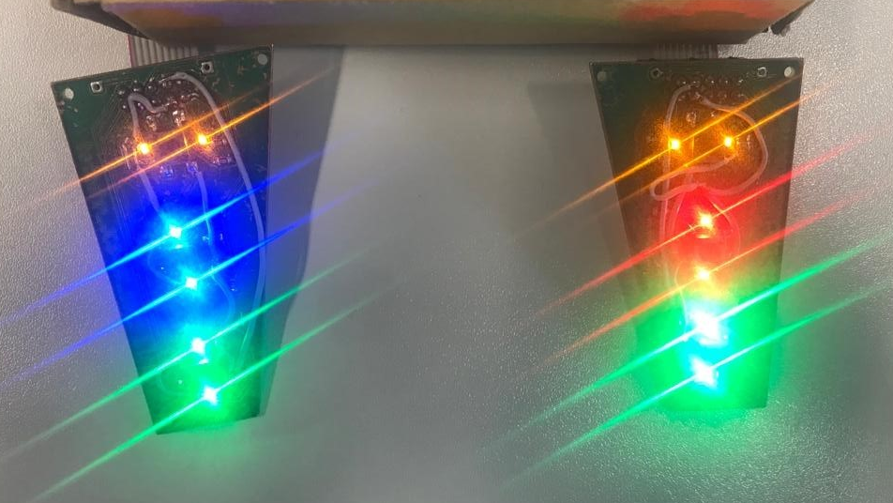
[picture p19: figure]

Abbildung 5: Tasterplatinen (JCS-BK_1046)

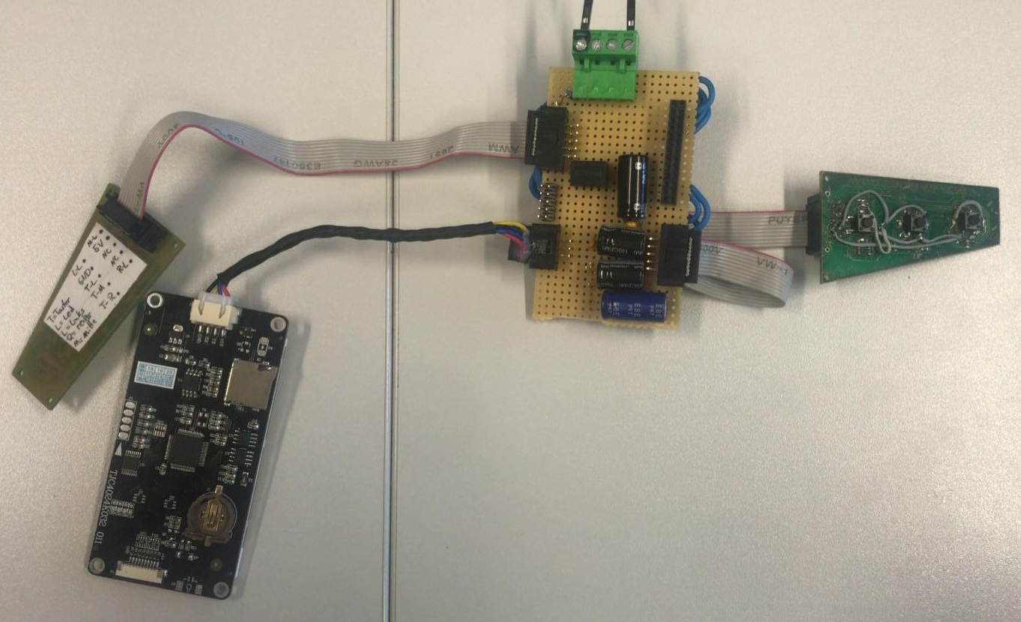
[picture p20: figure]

Abbildung 3: Adapterplatine verbunden mit Tasterplatine (JCS-BK_1046)

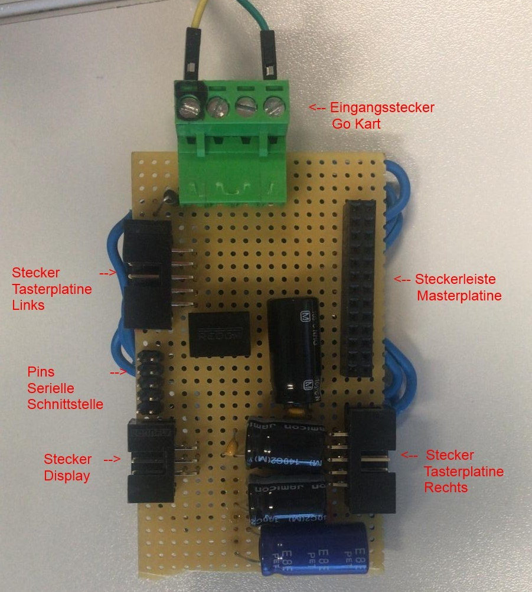
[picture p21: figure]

Abbildung 4: Adapterplatine (JCS-BK_1046)

### JCS-BK_1049_GO-KART Lichtanlage

Die Lichtanlage wurde von dem letzten Projekt (JCS-BK_1071) überarbeitet.

### JCS-BK_1071_GO-KART Blinker_Lenkrad_Anzeige

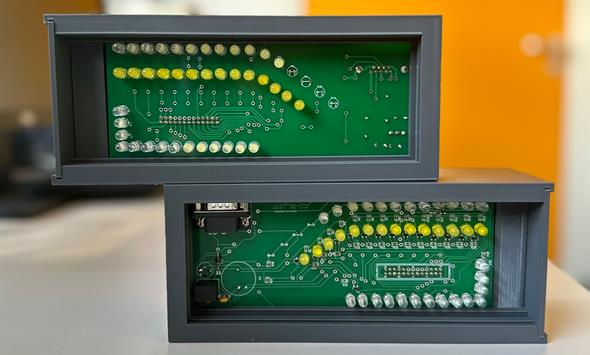
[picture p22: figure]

Abbildung 6: Frontlicht (JCS-BK_1071)

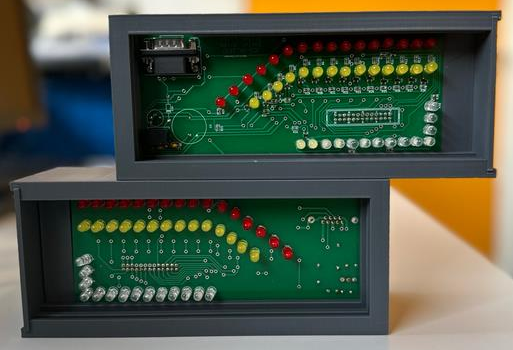
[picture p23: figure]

Abbildung 7: Rücklicht (JCS-BK_1071)

In Abbildung 8 sieht man die Masterplatine, welche in jedem Element eingebaut ist:

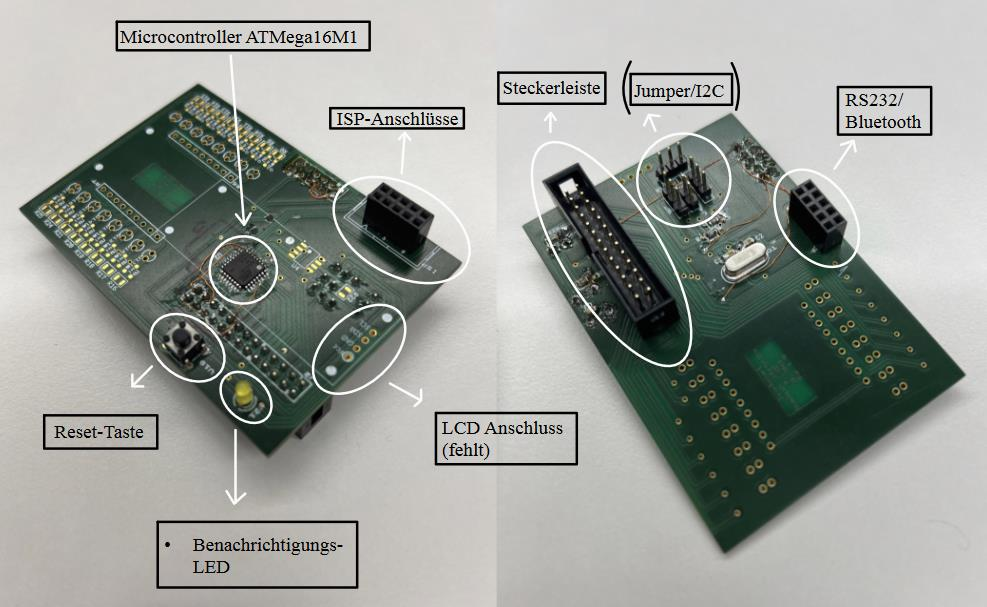
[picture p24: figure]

Abbildung 8: Masterplatine (JCS-BK_1071)

- Cockpit
- Frontlicht rechts und links
- Rücklicht rechts und links

Aus der Dokumentation des Vorgängers lässt sich schließen das die Front- und Rücklicht funktionsfähig sind.

Sofern ein Austausch durch den AT90CAN32 vorgenommen werden soll, kann die aktuelle Masterplatine nicht weiterverwendet werden. Da der AT90CAN32 über 64 Pins verfügt, während der bisher eingesetzte ATmega16M1 nur 32 Pins besitzt, ist die Anfertigung einer neuen Masterplatine erforderlich. Zudem ist der AT90CAN32 ausschließlich in einem SMD-Gehäuse erhältlich, wodurch die Verwendung eines Breadboards für den Prototypen ausgeschlossen ist.

# Ablauforganisation

Da die Zeit sehr knapp ist und das Cockpitdisplay von den anderen Projekten des Teams abhängig ist, muss man davon ausgehen das, das Projekt nicht vollständig abgeschlossen werden kann. Aus dieser Überlegung geht folgende Bearbeitungsreihenfolge hervor:

1. Bestandsaufnahme
2. Auswertungsprogramm in Auftrag geben
3. Licht
4. Bluetooth-Anbindung
5. CAN-Bus-Anbindung
6. Lenkrad
7. Cockpitdisplay

## Machbarkeitsanalyse

Kann ich | Muss ich erarbeiten
Programmierung von Mikrocontrollern | Bluetooth
I²C | CAN-Bus
3D-Druck | Ansteuerung des Displays
Planung und Fertigung von Platinen | Ansteuerung der Lichter
Office-Software Bedienung

Tabelle 3: Machbarkeitsanalyse

## Meilensteine

Start- datum | Ziel- datum | Zeit(h) | Thema (Aufgabe)
01.09.25 | 11.09.25 | | Festlegen des Themas und der Projektteams (Informationssammlung, Pflichtenheft zur Aufgabenfixierung, Aufgabenverteilung im Team und Anfertigung des Detailterminplans)
12.09.25 | 08.10.25 | 18 | Abgabe des Pflichtenhefts
| | | Statusermittlung Terminplanprüfung festlegen weiterer Schritte
| | | Schaltplan- und Layouterstellung / Programmierung von Modulen Testaufbau / Modultests / Dokumentation
| | | Abgabe der Draft 1 - Dokumentationsentwurf
| | | Statusermittlung Terminplanprüfung festlegen weiterer Schritte
| | | Schaltplan- und Layouterstellung / Programmierung von Modulen Testaufbau / Modultests / Dokumentation
| | | Programmtests, Dokumentation, Fehleranalyse, Fehlerbeseitigung
| | | Abgabe der Draft2-Dokumentation 7:35 keine Verlängerung
| | | Programmtests, Dokumentation, Fehleranalyse, Fehlerbeseitigung
| | | Präsentation des Projekts Weiterentwicklung
| | | Präsentation der Ergebnisse als Impress-Vortrag
| | | Präsentation der Zwischenstände am Tag der offenen Tür
| | | Abgabe des Projekts mit Abschluss-Dokumentation 24:00
| | | Leistungsüberprüfung / Produktabnahme

## Terminplan

Tabelle 4: Terminplan 01.09. - 19.09.2025

Tabelle 5: Terminplan 20.10. - 07.12.2025

Tabelle 6: Terminplan 08.12.2025 - 25.01.2026

Tabelle 7: Terminplan 26.01. - 15.03.2026

Tabelle 8: Terminplan 16.03. - 10.05.2026

# Auftragsbestätigung

Mit dieser Unterschrift bestätigt der Auftraggeber, dass das vorliegende Pflichtenheft inhaltlich geprüft und freigegeben ist. Es gilt damit als verbindliche Grundlage für die weitere Planung, Entwicklung und Umsetzung des Projektes. Änderungen und Erweiterungen nach der Unterzeichnung benötigen eine Vereinbarung zwischen Auftraggeber und Auftragnehmer.

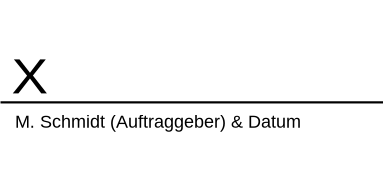
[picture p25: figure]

# Anhang

## Tagesziele

## Abbildungsverzeichnis

Tabelle 9: Tagesziele

Abbildung 1: Kommunikationsdiagramm 2

Abbildung 2: Display (Nextion NX8048K070) 3

Abbildung 3: Adapterplatine verbunden mit Tasterplatine (JCS-BK_1046) 7

Abbildung 4: Adapterplatine (JCS-BK_1046) 7

Abbildung 5: Tasterplatinen (JCS-BK_1046) 7

Abbildung 6: Frontlicht (JCS-BK_1071) 8

Abbildung 7: Rücklicht (JCS-BK_1071) 8

Abbildung 8: Masterplatine (JCS-BK_1071) 8

## Tabellenverzeichnis

Tabelle 1: Team 2

Tabelle 2: alte Projekte 6

Tabelle 3: Machbarkeitsanalyse 9

Tabelle 4: Terminplan 01.09. - 19.09.2025 11

Tabelle 5: Terminplan 20.10. - 07.12.2025 12

Tabelle 6: Terminplan 08.12.2025 - 25.01.2026 13

Tabelle 7: Terminplan 26.01. - 15.03.2026 14

Tabelle 8: Terminplan 16.03. - 10.05.2026 15

Tabelle 9: Tagesziele 17

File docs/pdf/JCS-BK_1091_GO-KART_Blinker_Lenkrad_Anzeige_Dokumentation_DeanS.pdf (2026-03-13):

## BERUFLICHES GYMNASIUM TECHNIK

JOHANN-CONRAD-SCHLAUN-BERUFSKOLLEG

### Dokumentation

### Go-Kart Blinker Lenkrad Anzeige

Dean Schneider

Auftraggeber: | Michael Schmidt
Projektleitung: | Henry Otto
Projektnummer: | JCS-BK_1091_GO-KART
Jahrgang: | GYT26
Fach: | Projekt mit Elektrotechnik und Informatik
Verfasser: | Dean Schneider
Projektstart: | 1. September 2025
Projektende: | 20. März 2026
Letzte Änderung: | 13. März 2026

## Abstract

For several years, students at the technical high school have been working on upgrading a go-kart by integrating systems typically found in modern cars. The individual modules communicate via a CAN bus network, similar to that used in real vehicles. Two microcontrollers from the AVR family are used throughout the system. The task is devided into multiple projects − one for each student.

This document describes the development of the light modules and the cockpit module. There is also a video showcasing the development. The lighting system consists of four modules, one for each corner of the vehicle. The two front modules support upper beam, lower beam, and daytime running lights, while the two rear modules provide tail, brake, and reverse lights.
The cockpit module includes a display, a horn, and several buttons mounted on the steering wheel. It serves as the central interface between the driver and the vehicle systems. The display presents information such as speed, battery charge, current gear, light status, and other relevant data. Using the steering wheel buttons and switches, the driver can control things like the driving direction, light mode, blinker direction, horn and gear.

All required tasks of this project were successfully completed. The service provider (TIO) did not finish the Java-based frontend; however, the serial communication interface has already been implemented. Since the other projects have not yet integrated CAN bus communication into their modules, communication between the cockpit and the other systems is currently not possible. In addition, a 3D-printed case for the display and caps for the buttons could be developed in the future.

## Kurzfassung

Seit mehreren Jahren arbeiten Schüler der gymnasialen Oberstufe Bereich Technik daran, ein Go-Kart durch die Integration von Systemen, die typischerweise in modernen Autos zu finden sind, aufzurüsten. Die einzelnen Module kommunizieren über CAN-Bus, ähnlich wie es in echten Fahrzeugen verwendet wird. Im gesamten System kommen zwei Mikrocontroller aus der AVR-Familie zum Einsatz. Die Aufgabe ist in mehrere Projekte unterteilt – eines für jeden Schüler.

Dieses Dokument beschreibt die Entwicklung der Lichtanlage, des Lenkrads und der Tachoanzeige. Des weiteren gibt es ein Video in dem die Entwicklung gezeigt wird. Die Lichtanlage besteht aus vier Modulen, eines für jede Ecke des Fahrzeugs. Die beiden vorderen Module unterstützen Fernlicht, Abblendlicht und Tagfahrlicht, während die beiden hinteren Module Rücklicht, Bremslicht und Rückfahrlicht liefern.
Das Cockpitmodul umfasst ein Display, eine Hupe und mehrere am Lenkrad angebrachte Taster. Es dient als zentrale Schnittstelle zwischen dem Fahrer und den Fahrzeugsystemen. Das Display zeigt Informationen wie Geschwindigkeit, Batterieladestand, aktueller Gang, Lichtstatus und andere relevante Daten an. Mit den Tasten und Schaltern am Lenkrad kann der Fahrer beispielsweise die Fahrtrichtung, den Lichtmodus, die Blinkerrichtung, die Hupe und den Gang steuern.

Alle gegebenen Aufgaben dieses Projekts wurden erfolgreich abgeschlossen. Der Dienstleister (TIO) hat das Java-basierte Frontend nicht fertiggestellt, jedoch wurde die serielle Schnittstelle bereits implementiert. Da die anderen Projekte die CAN-Bus-Kommunikation noch nicht in ihre Module integriert haben, ist eine Kommunikation zwischen dem Cockpit und den anderen Systemen derzeit nicht möglich. Darüber hinaus könnte in Zukunft ein 3D-gedrucktes Gehäuse für das Cockpit und Kappen für die Lenkrad-Taster entwickelt werden.

## Inhaltsverzeichnis

## 1 Einleitung

Diese Dokumentation richtet sich an Personen, welche auf dem Wissensstand der 12. Klasse berufliches Gymnasium Technik sind. Die Themen sind nach ihrer Priorität für das Nachschlagen geordnet. Das bedeutet, dass zunächst der aktuelle Aufbau (das Ergebnis) beschrieben wird, dies ist geeignet für Techniker welche keine interesse in den internen Einzelheiten ist. Anschließend die Entwicklung hin zum aktuellen Aufbau, dies ist das Kapitel für Personen, welche das Projekt weiterführen oder warten möchten. Schließlich die Grundlagen zur Bedienung der Software.

## 1.1 Projektziel

Um überhaupt erst mit dem Projekt zu beginnen müssten alle erhaltenen Hardware Produkte auf Funktion getestet. Die Dokumentationen der Vorgänger waren dabei oft falsch oder nicht hilfreich.
- Programm für Blinker-Module entwickeln
- animierter Blinker
- über UART steuerbar
- über CAN-Bus steuerbar
- Programm für Cockpit
- Anzeige auf Display und Einlesen von Tastern
- Kommunikation über CAN-Bus
- Platine für Cockpit welche das Display, die Taster, die Hupe und weitere Dinge verbindet. Alle Ziele wurden erreicht und sind unter dem Kapitel 2 Ergebnis (siehe S. 5) zu finden.

## 1.2 Hinweise zu diesem Dokument

Das hier genannte Cockpit-Display wird in anderen Dokumentationen Tacho, Tachodisplay oder einfach nur Display genannt.

Jeder Schaltplan in dieser Dokumentation entspricht der realität, das heißt Änderungen an der realen Cockpitplatine sind in den Schaltplänen aktualisiert, um Verwechslungsgefahr zu vermeiden.

Gesamte Anleitung für Linux um genau zu sein für die Arch Distribution.

MCU (Microcontroller Unit) entspricht Mikrocontroller.

Hexadezimalzahlen werden durch ein „h“ gekennzeichnet (z. B. FFh oder 003Bh).

## 1.3 Code Konventionen

- Einheitliche Einrückung mit 4 Leerzeichen (keine Tabs)
- Maximale Zeilenlänge von 80 Zeichen
- Variablen und Funktionen: snake_case
- Konstanten: UPPER_CASE
- Aussagekräftige Namen statt Abkürzungen (calculate_total statt calc)
- Kommentare richten sich nach dem Google Style C++ Guide (https://google.github.io/styleguide/cppguifde.html#Comments)

## 2 Ergebnis

Unter dem Kapitel Entwicklung befinden sich ausführliche Beschreibungen der im Folgenden genannten Themen.

## 2.1 Team

Dieses Projekt wird in enger Zusammenarbeit mit dem Team realisiert. So muss die Kommunikation abgesprochen werden. Die Verteilung der Aufgaben sieht wie folgt aus:

Name | Aufgabe
Henry Otto | Motoransteuerung und Auslesung der Pedalen
Iuri Merklein Muniz | Elektrische Bremse und Gangschaltung
Tammo Lohe | Ladeelektronik, Batterie und Solar
Dean Schneider | Lenkrad, Cockpitdisplay und die Beleuchtung

Tabelle 1: Team; Fahrer; Antrieb; Bremse; Ladeelektronik; Gangschaltung; Lenkrad; Blinker-Module; Versorgungsspannung freischalten; Zustand der Batterie; Vorwärts; Bremsepedal drücken; Bremsstärke anzeigen; Bremsstärke; Bremse anziehen; Feststellbremse lösen; Gang hochschalten; Gang anzeigen; aktuellen Gang; kein Ladekabel verbunden?; Gaspedaldrücken; Motordrehzahl erhöhen; Geschwindigkeit; rechts blinken; rechtes Blinkersymbol leuchtet; jeweils rechte Blinker einschalten

Abbildung 1: Kommunikation zwischen den Projekten im Sequenzdiagramm

Nachrichten an den Fahrer werden durch das Display visualisiert. Die meisten Nachrichten werden in
einem Interval gesendet und sind in Abbildung 1 nur vereinfacht dargestellt, die gesamte
Kommunikation ist dem CAN-Prokoll zu entnehmen (siehe 2.2 CAN-Protokoll, S. 7).

## 2.2 CAN-Protokoll

Dies zeigt alle Nachrichten innerhalb des Controller-Area-Network. Damit man weiß von welchen Blinker-Modul die Statusmeldung kam, sendet der jeweilige Blinker die eigene CAN-ID.

7

Tabelle 2: CAN-Protokoll

Erstell von Dean Schneider (GYT26) Version 0.4.0

Legende:

MSB | least significant bit
LSB | most significant bit
| 1. Datenbyte
an CAN-ID | Interval | Gruppe | Nachricht an Gerät | von Gerät | Bit 7 | Bit 6 | Bit 5 | Bit 4 | Bit 3 | Bit 2 | Bit 1 | Bit 0
0x703 | ~1 Hz | Status | Cockpit | jedem Blinker | | | | | voll Licht oben | leicht Licht oben | Blinker | Licht unten
0x702 | | Status | Antrieb | Bremse | MSB | Bremsenstärke von 0 bis 255, großer Wert für starke Bremsung | | | | | | LSB
0x701 | | Status | Antrieb und Cockpit | Bremse / Gangschaltung | 0: Stehen 1: Fahren | (A) Fußbremse | (A) Handbremse | | (B) 3. Gang | (B) 2. Gang | (B) 1. Gang | (B) Neutralgang
0x605 | | Anzeige | Cockpit | Gangschaltung | MSB | Geschwindigkeit von 0 bis 255 | | | | | | LSB
0x604 | | Anzeige | Blinker vorne rechts | Cockpit | | | | | Fernlicht | Abblendlicht | Blinker | Tagfahrlicht
0x603 | | Anzeige | Blinker vorne links | Cockpit | | | | | Fernlicht | Abblendlicht | Blinker | Tagfahrlicht
0x602 | | Anzeige | Blinker hinten rechts | Cockpit | | | | | Bremslicht | Rücklicht | Blinker | Rückfahrlicht
0x601 | | Anzeige | Blinker hinten links | Cockpit | | | | | Bremslicht | Rücklicht | Blinker | Rückfahrlicht
0x302 | | Ladeelektronik | Ladeelektronik und Cockpit | Antrieb mit Pedale | MSB | Strom von 0 bis 255 | | | | | | LSB
0x301 | | Ladeelektronik | Antrieb und Cockpit | Ladeelektronik | | | Batterieladen | 4/4 Batterie | 3/4 Batterie | 2/4 Batterie | 1/4 Batterie | leere Batterie
0x202 | | Gangschaltung | Gangschaltung | Cockpit | | | | | 3. Gang | 2. Gang | 1. Gang | Neutralgang
0x201 | | Bremse | Bremse und Cockpit | Pedale (Antrieb) | MSB | Bremsenstärke von 0 bis 255, großer Wert für starke Bremsung | | | | | | LSB
0x101 | | Antrieb | Antrieb | Cockpit | | | | | | | 0: Vorwärts 1: Rückwärts | 0: Stop 1: Start
0x0.. | Fehler

Blinker senden ihre CAN-ID in den 2. (MSB) bis 5. Byte der Statusnachrichten Rot markiert, dass nur ein Bit 1 sein darf,
zusätzlich wird in Gruppen unterteilt, z. B. (A) oder (B).

Dieses Diagramm zeigt alle CAN-Nachrichten aus Tabelle 2 (siehe S. 7) und an wenn sie gerichtet sind. Gestrichelte Pfeile sind dabei Status- oder Bestätigungsnachrichten.

8

Abbildung 2: Kommunikationsdiagramm des CAN-Protokolls

## 2.3 Cockpit


Die untere Platine wurde in diesem Projekt erstellt. Die grüne LED zeigt an ob 5V anliegen. Dabei werden die Taster werden wie in dem Bild links in dem Lenkrad befestigt.

9

Abbildung 3: Cockpitplatine mit allen Geräten angeschlossen


Abbildung 4: Schaltplan der Cockpitplatine Rev 2


Abbildung 6: Leiterbahnen (bottom) der Cockpitplatine Rev 2

Abbildung 5: Bauteilansicht (top) der Cockpitplatine Rev 2
Der einzige Fehler welcher korrigiert werden musste, ist eine Brücke zwischen MOSI und RXD0 bzw. MISO und TXD0. Diese Änderung ist in diesem
Schaltplan bereits korrigiert. Jeder Schaltplanausschnitt in dieser Dokumentation entspricht der Realität. Eine Besonderheit des Schaltplanes (siehe
Abbildung 4, S. 10) ist die Verwendung von Labels, so sind zum Beispiel „Vcc (5V)“ der LED und alle weitere Anschlüsse mit der Bezeichnung „Vcc
(5V)“ in Wirklichkeit miteinander Verbunden.

Name | Go-Kart_Cockpit
Passowort | 1234
Baudrate | 9600 bit pro Sekunde

Tabelle 3: Cockpit Bluetooth-Modul Einstellungen
Das Cockpit, sprich der AT90CAN32 Microcontroller des Cockpits kann über CAN-Bus mit den anderen Projekten und den Blinkern kommunizieren. Außerdem gibt es eine Ausgabe über Bluetooth. Wie man über Bluetooth sendet, wird später erklärt (siehe 4.2 UART Übertragung, S. 55).

Abbildung 7: Bluetooth-Modul auf der Cockpitplatine

## 2.4 Blinker-Module

Name | Go-Kart_Blinker
MAC-Adresse | 00:21:13:01:54:0F
Passowort | 1234
Baudrate | 9600 bit pro Sekunde

Tabelle 4: Blinker Bluetooth-Modul Einstellungen

Diese Blinker-Module habe ich fertig erhalten. Die Platine wurde von Christoph Waßmuth in dem Projekt JCS-BK_1025 entwickelt.

Alle Blinker-Module wurden auf Funktion überprüft. Dabei haben alle funktioniert bis auf vorne links, wahrscheinlich hat dieser noch nicht die Brücke welche bei den anderen Hinzugefügt wurde.

Jedes Blinker-Modul kann einzelnt über CAN-Bus oder per Bluetooth auch mit Textbefehlen gesteuert werden. Wie man über Bluetooth sendet, wird später erklärt (siehe 4.2 UART Übertragung, S. 55). Durch sendet des Buchstaben „h“ erhält man eine Liste der möglichen Befehle. Alle vier Blinker-Module teilen sich ein Bluetooth-Modul.

Hilfe Ausgabe von dem Blinker-Modul hinten links:
info: JCS-BK_1091_GO-KART von Dean Schneider (GYT26)
info: Blinker-Modul hinten links mit CAN-ID: 0x00000601 info: State Nachrichten werden an 0x00000703 gesendet. info: UART Befehle:
info: an='1', aus='2': Blinker
info: an='3', aus='4': Rueckfahrlicht
info: '5': Ruecklicht
info: '6': Bremslicht
info: '7': kein oberes Licht

Abbildung 8: Alle vier Blinker-Module

## 2.5 Dateistruktur

Der Quellcode und weitere Dateien des Projektes sollten von dem Projektleiter bereitgestellt werden. Die Diagramme wurden mit PlantUML erstellt, die Rohdateien dazu sind in den .puml Dateien zu finden.

├── CMakeLists.txt
├── docs
│ | ├── datasheets
│ | │ | ├── at90can.pdf
│ | │ | ├── CSR_BC417.pdf
│ | │ | └── HC-06.pdf
│ | ├── images
│ | │ | ├── can-protokoll.puml
│ | │ | ├── Cockpitplatine_real.xcf
│ | │ | ├── communication_sequence.puml
│ | │ | ├── go-kart.png
│ | │ | ├── PAP_CAN.odg
│ | │ | ├── PAP_CAN.svg
│ | │ | └── timing_diagram.puml
│ | └── tables
│ | ├── alte_projekte.ods
│ | ├── can_protokoll.ods
│ | ├── tagesziele.ods
│ | └── terminplan.ods
├── lib
│ | ├── avr-can-lib
│ | │ | ├── can.h
│ | │ | ├── CMakeLists.txt
│ | │ | ├── demo
│ | │ | │ | ├── can.h
│ | │ | │ | ├── config.h
│ | │ | │ | ├── main.c
│ | │ | │ | └── makefile
│ | │ | ├── README.md
│ | │ | └── src
│ | │ | | ├── at90can_buffer.c
│ | │ | | ├── at90can.c
│ | │ | | ├── at90can_disable_dyn_filter.c
│ | │ | | ├── at90can_error_register.c
│ | │ | | ├── at90can_get_buf_message.c
│ | │ | | ├── at90can_get_dyn_filter.c
│ | │ | | ├── at90can_get_message.c
│ | │ | | ├── at90can_private.h
│ | │ | | ├── at90can_send_buf_message.c
│ | │ | | ├── at90can_send_message.c
│ | │ | | ├── at90can_set_dyn_filter.c
│ | │ | | ├── at90can_set_mode.c
│ | │ | | ├── can_buffer.c
│ | │ | | ├── can_buffer.h
│ | │ | | ├── can_private.h
│ | │ | | ├── config.h

│ | │ | ├── doxyfile
│ | │ | ├── makefile
│ | │ | ├── mcp2515_buffer.c
│ | │ | ├── mcp2515.c
│ | │ | ├── mcp2515_defs.h
│ | │ | ├── mcp2515_error_register.c
│ | │ | ├── mcp2515_get_dyn_filter.c
│ | │ | ├── mcp2515_get_message.c
│ | │ | ├── mcp2515_private.h
│ | │ | ├── mcp2515_read_id.c
│ | │ | ├── mcp2515_regdump.c
│ | │ | ├── mcp2515_send_message.c
│ | │ | ├── mcp2515_set_dyn_filter.c
│ | │ | ├── mcp2515_set_mode.c
│ | │ | ├── mcp2515_sleep.c
│ | │ | ├── mcp2515_static_filter.c
│ | │ | ├── mcp2515_write_id.c
│ | │ | ├── sja1000_buffer.c
│ | │ | ├── sja1000.c
│ | │ | ├── sja1000_defs.h
│ | │ | ├── sja1000_error_register.c
│ | │ | ├── sja1000_get_message.c
│ | │ | ├── sja1000_private.h
│ | │ | ├── sja1000_send_message.c
│ | │ | ├── sja1000_set_mode.c
│ | │ | ├── spi.c
│ | │ | ├── spi.h
│ | │ | └── utils.h
│ | └── usart
│ | ├── CMakeLists.txt
│ | ├── include
│ | │ | ├── usart_config.h
│ | │ | └── usart.h
│ | └── src
│ | | └── usart.c
├── LICENSE
├── README.md
└── src
├── blinker
│ | ├── blinker_controller.c
│ | ├── hal.h
│ | ├── main.c
│ | └── uart_AM16M1.h
└── cockpit
├── cockpit_display.c
├── cockpit_display.h
├── hal.h
└── main.c

## 2.6 CAN-Bus

CAN-Bus Baudrate | 125 kbit pro Sekunde

Tabelle 5: CAN-Bus Einstellungen

Abbildung 9: männlicher CAN D-Sub Anschluss nach CiA® 106 (Quelle: PCAN-USB Anleitung)

## 2.7 Mikrocontroller

### 2.7.1 ATmega16M1

Für die Lichtanlage wird der ATmega16M1 Mikrocontroller verwendet.

Die wichtigsten Eigenschaften des ATmega16M1:

- 16 KB Flash, 1 KB SRAM, 512 byte EEPROM
- Hardware CAN-Controller
- Hardware UART mit LIN
- 2x 8-bit Timer und 1x 16-bit Timer für PWM
- Analog-Digital-Wandler


Abbildung 10: Stecker zum
Programmieren des ATmega16M1


Abbildung 11: Oberseite des ATmega16M1


Abbildung 12: Unterseite des ATmega16M1


### 2.7.2 AT90CAN32

Die Platine mit dem AT90CAN32 Mikrocontroller wird für das Cockpit-Display und das Lenkrad verwendet. Da es die zentrale Steuereinheit für dieses Projekt ist, wird sie auch als Masterplatine bezeichnet. Das Projekt JCS-BK MS-001 enthält Schaltpläne zur Masterplatine. Pläne zur Addon-Platine, dass heißt dort wo die serielle und ISP Verbindung angeschlossen wird, lassen sich unter JCS-BK MS-003 finden.

Die wichtigsten Vorteile des AT90CAN32 gegenüber dem ATmega16M1 für dieses Projekt sind:
- zwei USART-Schnittstellen gegenüber einer beim ATmega16M1
- stärkerer CAN-Controller mit mehr Funktionen und Message Objects:
– | AT90CAN32: 15 Full Message Objects
– | ATmega16M1: 6 Message Objects
- Hardware I2C-Controller

Der AT90CAN32 wurde explizit für seine zwei USART-Schnittstellen verwendet.

Abbildung 15: Masterplatine mit AT90CAN32 (MS-001)

Abbildung 13: Anschlüsse des
AT90CAN32 (Quelle: Schaltplanausschnitt von MS-001)

Abbildung 14: Masterplatine mit AT90CAN32 (MS-001)

## 3 Entwicklung

In diesem Kapitel wird der Prozess wie es Ergebnis kam dargestellt. Der aktuelle Stand des Projektes befindet sich im Kapitel 2 Ergebnis (Beginn S. 5).

## 3.1 Programmierer

Ein Arduino besitzt einen Bootloader welcher den Eingang des UART in den Speicher schreibt, er programmiert sich also selbst. Allerdings besitzt der AVR MCU (AT90CAN32) von der Masterplatine keinen Bootloader, er wird über ISP (In-System Programming) programmiert.

Beim Kauf eines Programmierers ist darauf zu achten, dass er eine Open-Source Firmware hat, zum Beispiel USBasp.

Falls man nicht weiß welche Programmierer-Firmware man hat, kann man diese über die ID herausfinden:
$ lsusb
Zum Hochladen wird avrdude verwendet dasselbe Tool wie Microchip Studio verwendet. Als Erstes muss das Paket avrdude installiert werden. Dieses Paket ist nicht unbedingt überall vorhanden. Falls ein Paket nicht vorhanden ist kann man es auch immer über eine normale Intersuche finden und herunterladen (https://github.com/avrdudes/avrdude/releases). Zum Beispiel auf Arch mit:
$ sudo pacman -S avrdude
Anschließend kann man sich mit diesem Befehl alle voreingestellte Programmierer-Konfigurationen ausgeben lassen:
$ avrdude -c ?

Abbildung 16: ISP Pinbelegung (Quelle: wikipedia.org von osiixy erstellt)

## 3.2 Erste Schritte mit Masterplatine


Bevor man komplexe Programme programmiert sollte man erstmal die Programmier-Schnittstelle überprüfen. In diesem Beispiel wird TX zwischen High und Low gewechselt. Mein USB-zu-Seriell Gerät hat eine LED für RX, darüber kann ich den Spannungswechsel sehen. Kurz gesagt wird eine blinkende LED zum Feststellen der Funktion verwendet.

Warnung: In Abbildung 17 ist der Aufbau zu sehen. Es ist wichtig zu überprüfen ob der Programmierer eine Spannung liefert (z. B. 5V), denn dann sollte die Spannungsversorgung des USB-zu-Seriell Adapters von der Masterplatine getrennt werden. Oft ist dies nicht nötig, es reduziert jedoch das Risiko eines Schadens durch Ausgleich-Ströme.

Hier ist der Code zum Blinken lassen der RX LED (siehe 4.1 Kompilieren und Hochladen, S. 54): #include <avr/io.h>
#include <util/delay.h>

static const uint8_t TXD1 = PD3;

int main(void) {
DDRD = 1 << TXD1;

while (1) {
PORTD ^= 1 << TXD1;
_delay_ms(500);
}
}
Die Schritte zum hochladen werden in den Grundlagen erklärt (siehe 4.1 Kompilieren und Hochladen,
S. 54).

Abbildung 17: Masterplatine mit serieller und ISP Verbindung

## 3.3 Entwicklung mit HAL

Dieses Projekt verwendet für jeweils den Blinker und das Cockpit ein Hardware-Abstraktions-Layer (https://en.wikipedia.org/wiki/Hardware_abstraction). Dadurch wird der Code lesbarer und Fehler werden vermieden. Die besonderheit ist sowohl der Port als auch der Bit/Pin werden in einem Define gespeichert und anschließend mit Makros wieder extrahiert. Der zuvor gezeigte Blinktest würde dann so in eine hal.h C-Datei geschrieben werden:
#ifndef HAL_H

#define HAL_H

#include <avr/io.h>

// Beispiel: PORTC PC6 => C, 6

#define UART1_TX D, 3

#define _SET2(port, bit) PORT##port |= (1 << bit) #define _GET2(port, bit) ((PIN##port >> bit) & 1) #define _RESET2(port, bit) PORT##port &= ~(1 << bit) #define _TOGGLE2(port, bit) PORT##port ^= (1 << bit) #define _SET_INPUT2(port, bit) DDR##port |= (1 << bit) #define _SET_OUTPUT2(port, bit) DDR##port |= (1 << bit)

#define SET(port_comma_bit) _SET2(port_comma_bit) #define GET(port_comma_bit) _GET2(port_comma_bit)

#define RESET(port_comma_bit) _RESET2(port_comma_bit)

#define TOGGLE(port_comma_bit) _TOGGLE2(port_comma_bit) #define SET_INPUT(port_comma_bit) _SET_INPUT2(port_comma_bit) #define SET_OUTPUT(port_comma_bit) _SET_OUTPUT2(port_comma_bit)

#define _P2(port, bit) (1 << bit)

#define _P(port_comma_bit) _P2(port_comma_bit)

void hal_init(void) {
// set output pins
DDRD = _P(UART1_TX);
}

#endif

Anschließend kann man Pins wie folgt ansteuern und auch auslesen (main.c): #include <avr/io.h>
#include <util/delay.h>

#include "hal.h"

int main(void) {
hal_init();

while (1) {
TOGGLE(UART1_TX);
_delay_ms(500);
}
}

## 3.4 Bluetooth-Modul


In Abbildung 18 ist das verwendete Bluetooth-Modul zu sehen. Bei der grünen aufgelöteten Platine handelt es sich um den HC-06 mit dem CSR BC417BQN (Bluetooth Chip). Der HC-06 unterscheidet sich vom HC-05, indem er nur als Slave fungieren kann. Das bedeutet der HC-06 kann nicht ein Gerät
(z. B. Laptop) suchen und sich mit ihm Verbinden. Zu erkennen ist der HC-06 daran, dass nur 4 Pins herausgeführt sind.

Die Pins TX und RX fungieren als UART Schnittstelle.

PIN | Beschreibung
RX (3,3V) | Receive – Eingang UART des Moduls, benötigt einen Spannungsteiler
TX | Transmit – Ausgang UART des Moduls
GND | Verbindung zu GND
5V | +5V Versorgungsspannung

### 3.4.1 Test und konfigurieren mit USB-zu-Seriell-Konverter

Das Bluetooth-Modul wird mit dem USB-zu-Seriell-Konverter verbunden. Es sind keine Widerstände nötig da der Konverter mit 3,3 V arbeitet.

Bluetooth-Modul | USB-zu-Seriell-Konverter
RX | TX
TX | RX
GND | GND
5V | +5V

Die LED des Bluetooth-Moduls sollte blinken, sobald die Spannungsversorgung hergestellt wurde. Dies bedeutet das auf Verbindung gewartet wird.

Abbildung 18: Bluetooth-Modul mit HC-06 Oberseite
(Quelle: roboter-bausatz.de) | Abbildung 19: Bluetooth-Modul mit HC-06 Unterseite (Quelle: roboter-bausatz.de)

Nun können die Befehle zum Konfigurieren über UART (siehe 4.2 UART Übertragung, S. 55) mit einer Baud-Rate von 9600 bps übertragen werden. Beim HC-06 kann kein „AT Command Mode“ aktiviert werden. Er befindet sich immer im Kommando-Modus, wenn keine Verbindung besteht was an dem Blinken der LED zu erkennen ist.

Befehl senden | Beispiel | Rückgabe vom Modul
AT | | OK
AT+VERSION | | OKlinvorV1.8
AT+NAME<Name> | AT+NAMEBlinker | OKsetname
AT+PIN<PIN> | AT+PIN1234 | OKsetPIN

Es gibt weitere Befehle (siehe Datenblatt). So ist es zum Beispiel möglich die BAUD-Rate zu verändern, allerdings reicht 9600 bps völlig für den UART gebrauch aus und eine Änderung kann Projekt verwirren.

Schließlich kann man sich mit einem anderen Computer über Bluetooth Verbinden und seriell Daten an den Computer mit der UART Verbindung senden (siehe 4.2 UART Übertragung, S. 55).

### 3.4.2 Schaltung mit Mikrocontroller


Der TX Pin des Bluetooth-Moduls wird über eine Diode geleitet, da der MCU noch nicht initialisiert sein könnte und damit der RX des MCU High ist und TX Low, dadurch entsteht ein Kurzschluss. Der TX Pin des MCU wird über einen Spannungsteiler angeschlossen da der MCU mit 5V und das Modul mit 3.3 V arbeitet. Im Folgenden wird der Spannungsteiler dimensioniert.

Die Eingangsspannungen beziehen sich auf den CSR BC417BQN.

Abbildung 20: Bluetooth-Modul Schaltung mit Arduino

Schaltplanausschnitt 1: Anschluss des Bluetooth-Modul an die Masterplatine


Schließlich kann man die UART-Ausgabe über Bluetooth auslesen und Daten an den MCU über
UART senden (siehe 4.2 UART Übertragung, S. 55).
Warnung: Hochladen über den Bootloader wird nicht funktionieren da ein Reset benötigt wird.

## 3.5 Blinker-Modul


In Abbildung 22 sieht man das Blinker-Modul mit der Microcontroller-Platine und wie das Bluetooth-Modul angeschlossen. Bei dem Bluetooth-Modul ist zu beachten, dass der Winkel nach innen zeigt.

### 3.5.1 Berechnung des Timers

Nach der Norm ECE 6.4 muss die Lampe für die Fahrtrichtungsanzeige mit einer Frequenz von 1,5 Hz den Zustand wechseln, mit einer Tolleranz von 0,5 Hz. Angeschalten gilt die Lampe, wenn 95% der LEDs angeschalten sind, dies ist nur der Fall, wenn alle 14 LEDs leuchten.

Aufgrund das der Blinker animiert ist und sonst zu schnell durchlaufen würde, wurde eine etwas geringere Frequenz gewählt.

Das folgende Signalzeitdiagramm zeigt den zeitlichen Verlauf der LEDs An bzw. Auszustände. Bei der Programmierung wird ein Timer mit Interrupt verwendet. ISR steht dabei für die Interrupt-Service-Routine. Man kann auch sagen jedes mal wenn ISR auf 1 geht findet ein Wechsel statt, sei es eine LED die oder aus geht oder einfach nichts tun.

Gesucht bei der Berechnung ist die Frequenz für den Timer.

Abbildung 22: Innenleben des Blinker-Moduls hinten rechts
Abbildung 21: Blinker auf Go-Kart positioniert

27

Abbildung 23: Signalzeitdiagramm für Blinker-LEDs

ISR

### 1. L ED

### 2. L ED

### 3. L ED

### 4. L ED

### 5. L ED

### 6. L ED

### 7. L ED

### 8. L ED

### 9. L ED

10 . LE D

11 . LE D

12 . LE D

13 . LE D

14 . LE D
43 ms | 346 ms
0 | 50 | 100 | 150 | 200 | 250 | 300 | 350 | 400 | 450 | 500 | 550 | 600 | 650 | 700 | 750 | 800 | 850 | 900 | 950 | 1000 | 1050 | 1100

Die in Abbildung 23 zusehenden Zeiten ergeben sich für 43 ms aus 1/fTimer und 346 ms ist TH.


Um die Anzahl der benötigten Aufrufe nges der Interrupt-Service-Routine zu finden, braucht man die Anzahl der Aufrufe in dem alle LEDs angeschalten sein sollen nH. Diese wurden durch aufstellen eines Verhältnisses gefunden.

Es steht nur noch der 8-Bit Timer0 zur Verfügung, da der 16-Bit Timer1 für das PWM verwendet wird. Mit 8-Bit kann man über die Hardware höchstens eine 255er Teilung erreichen, das reicht nicht für 23,1 Hz, daher muss zusätzlich eine Software Teilung stattfinden. Timer0 wird ebenfalls für die intervale Sendung von CAN-Nachrichten verwendet. Schließlich muss man Werte finden wo ein

So würde man den Timer mit den Registern Konfigurieren:
TCCR0A = 1 << WGM01; // reset Timer-Wert wenn OCR0A gleich ist
TCCR0B = 1 << CS02 | 1 << CS00;
OCR0A = 84;
Da die Interval-Nachrichten mit 1 Hz versendet wird, wäre die Initialierung davon wie folgt: OCR0B = 186;

Die Interrupt-Service-Routine sieht verkürzt so aus:
ISR(TIMER0_COMPA_vect) {
// timer frequency / SOFT_PRESCALER = frequency
static const uint8_t SOFT_PRESCALER = 8; // about 23.25 Hz

bc_interrupt_count++;

if (bc_interrupt_count != SOFT_PRESCALER) {
return;
}

bc_interrupt_count = 0;

switch (bc_current_stage) { case 0:
SET(LED_BLINKER_0);
break;
case 1:
SET(LED_BLINKER_1);
break;
case 13:
SET(LED_BLINKER_13);
break;
}

if (bc_current_stage == 14 + (7 - 1)) { reset_blinker_leds();
RESET(LED_BLINKER_0);
}

bc_current_stage++;

// 14 LEDs, 11 iterations with all enabled if (bc_current_stage >= 14 + 7) { bc_current_stage = 0;
}
}

## 3.6 CAN-Bus


Der CAN-Bus (Controller Area Network) ist ein serielles Kommunikationssystem, das vor allem in Fahrzeugen sowie in Industrie- und Automatisierungssystemen eingesetzt wird. Mehrere Steuergeräte, sogenannte Nodes, sind dabei parallel an eine gemeinsame Busleitung angeschlossen und können über diese miteinander Daten austauschen. Die Kommunikation erfolgt über zwei Leitungen, CAN-High und CAN-Low, auf denen ein differenzielles Signal übertragen wird. Dadurch ist das System relativ unempfindlich gegenüber elektromagnetischen Störungen.

Damit die Signalübertragung stabil funktioniert, werden an beiden Enden der Busleitung Abschlusswiderstände eingesetzt. Diese haben typischerweise einen Widerstandswert von 120 Ω und verhindern Signalreflexionen auf der Leitung, die sonst zu Übertragungsfehlern führen könnten. In Abbildung 24 sind die beiden Abschlusswiderstände sowie mehrere angeschlossene Nodes dargestellt, die über CAN-High und CAN-Low mit dem Bus verbunden sind. Abzweigungen können über längere Distanz zu Problemen führen.

Die Kommunikation auf dem CAN-Bus erfolgt über sogenannte CAN-Frames, die die eigentlichen Daten übertragen. Ein Frame besteht aus mehreren Feldern, unter anderem einer Identifier-ID, die die Priorität der Nachricht festlegt, dem Datenfeld, in dem die Nutzdaten übertragen werden, sowie einer CRC-Prüfsumme, mit der Übertragungsfehler erkannt werden können. Abbildung 25 zeigt beispielhaft den Aufbau eines vollständigen CAN-Frames mit ID-, Daten- und CRC-Bereich.

Abbildung 25: komplettes CAN frame Beispiel (Quelle: Canis Automotive Labs Ltd)

Abbildung 24: CAN bus elektrische Beispiel Topologie mit Abschlusswiderständen (Quelle: Stefan-Xp Wikipedia Nutzer)

### 3.6.1 Anschluss


CAN-Bus wird mit einem D-Sub 9 Stecker bzw. Kabel angeschlossen. Dieses Kabel liefert ebenfalls eine 0V und 24V Leitung. In Abbildung 1 sieht man das angeschlossene CAN-Bus-Kabel.

Abbildung 27: männlicher CAN D-Sub Anschluss nach CiA® 106 (Quelle: PCAN-USB Anleitung)

Abbildung 26: Blinker-Modul mit D-Sub Kabel

3.6.2 Beispiel-Programm; CAN Initialisieren; Initialisierung erfolgreich?; UART Initialisieren; Fehlermeldung; erfolgreich ?; Interrupts aktivieren; Sende Testnachricht

Dieses Beispiel-Programm stellt alle benötigten CAN-Bus funktionen dar. Die erhaltene CAN-
Nachricht an die ID=00001234h wird wieder zurückgeschickt, also ein Echo.

Start CAN-Test

CAN Filter setzen
(akzeptiere nur an ID: 1234h)

Sende Nachricht
zurück, falls eine
erhalten wurde

eine Sekunde warten

Ende CAN-Test

Abbildung 28: PAP zu dem CAN Testprogramm

#include "can.h"

#include "usart.h"

#include <avr/interrupt.h> #include <avr/io.h>

#include <util/delay.h>

int main(void) {
uart0_init(BAUD_CALC(9600UL));

if (!can_init(BITRATE_125_KBPS)) { uart0_puts("error: while can initialization\r\n"); while (true);
}

can_filter_t can_filter = {
.id = 0x00001234,
.mask = 0x1FFFFFFF,
.flags.extended = 0x3, // filter with extended id
.flags.rtr = 0x2, | // receive both RTR and normal
};

if (!can_set_filter(0, &can_filter)) {
uart0_puts("error: while setting can message filters\r\n"); while (true);
}

const can_t msg = {
.id = 0x12340000,
.flags.extended = true,
.flags.rtr = false,
.length = 1,
.data = {0xAA},
};

sei();

while (1) {
if (can_send_message(&msg) == 0) { uart0_puts("error: can_send_message\r\n"); continue;
}

can_t received_command;

if (can_get_message(&received_command)) { received_command.id = 0x12340000; can_send_message(&received_command); // echo for testing }

_delay_ms(1000);
}
}

## 3.7 Erstes Display (Tacho)

Eigentlich sollte das NX8048K070_011C Display von Nextion verwendet verwenden. Allerdings war ich direkt zu Beginn des Projektes unaufmerksam und habe aus versehen an das 5V Display 14V angeschlossen, das Display leuchtete bis die Spannungsversorgung entfernt wurde. Der Spannungsregler des Displays ist beschädigt und eventuell auch weitere Bauteile. Diese müssten ausgetauscht werden, wobei sich die Frage stellt, ob sich der Zeitaufwand lohnt, insbesondere da es sich um SMD Bauteile handelt und man nicht eindeutig die Bauteilbezeichnung lesen kann.

Nun muss das vorherige Display, welches allerdings von JCS-BK_1046 bereits gestaltet und eingestellt wurde, verwendet werden.

Abbildung 29: Nextion Display (NX8048K070_011C)

Abbildung 30: Ersatz Bauteil suche für Spannungsregler (Quelle: https://smd.yooneed.one)

## 3.8 Cockpit-Display (Tacho)

Das Display ist von Nextion und wird mit der Nextion typischen Software programmiert/eingestellt. Auf dem Glass befindet sich ein Riss von einem Vorgänger. Christian Barth (JCS-BK_1046) hat das Display gestaltet. Um die Symbole oder Zahlen zu ändern werden Befehle seriell mit einer Baudrate von 9600 bit/s gesendet (siehe 4.2.2 Rohdaten übertragen, S. 55).

### 3.8.1 Befehle

Funktion | ID | Wertebereich
linker Blinker | bL.pic | ausgeschalten | 0 | angeschalten | 1
rechter Blinker | bR.pic | ausgeschalten | 2 | angeschalten | 3
Warnblinker | warnB.pic | ausgeschalten | 15 | angeschalten | 16
Scheinwerfer | light.pic | Abblendlicht Standlicht | 17 19 | Fernlicht | 18
Drehzahl (Umdrehungen pro Minute) | rpm1.pic rpm2.pic rpm3.pic | Hunderter Zehner Einer | 4 − 13 | Index 4 entspricht 0 und Index 13 entspricht 9
Geschwindigkeit (km/h) | speed1.pic speed2.pic | Zehner Einer
gefahrene Distanz | dis1.pic dis2.pic dis3.pic | Hunderter Zehner Einer
eingelegter Gang | gear.pic | Neutralgang zweiter Gang | 14 6 | erster Gang dritter Gang | 5 7
Batterie-Zustand | battery.pic | leer 2/4 4/4 | 20 22 24 | 1/4 3/4 wird geladen | 21 23 25

Abbildung 31: Cockpit-Display (NX4024K032)

Funktion | ID | Wertebereich
Gaspedal | throttle.val | 0 − 100
Bremspedal | brake.val | 100 − 0

Tabelle 6: Befehle für das Cockpit-Display

Alle angegebene Befehle bis auf „gefahrene Distanz“ wurde mit einem Testprogramm überprüft.

So kann man zum Beispiel mit dieser Nachricht an das Display den linken Blinker einschalten: $ stty -F /dev/ttyUSB0 9600
$ printf 'bL.pic=1\xFF\xFF\xFF' > /dev/ttyUSB0
Erklärung dieser Befehle lässt sich unter 4.2.2 Rohdaten übertragen (siehe S. 55) finden.

Mit AVR-C könnte das so realisiert werden:
uart_puts("bL.pic=1\xFF\xFF\xFF");

### 3.8.2 Beispiel-Programm

Dieses Beispiel-Programm lässt in Zeitabständen verschiedene Symbole und Zahlen auf dem Cockpit-Display anzeigen. Die Übertragung findet über UART statt. Um dieses Programm zu benutzen muss die Bibliothek-Datei „cockpit_display.h“ im selben Ordner wie die Main-Datei liegen. Die Bibliothek verwendet STB-Library-Stil, deswegen muss „COCKPIT_DISPLAY_IMPLEMENTATION“ vorher definiert werden.

In diesem Projekt wird die Bibliothek AVR-UART-lib von jnk0le (https://github.com/jnk0le/AVR-UART-lib) verwendet.

#include "usart.h"

#include <util/delay.h>

#include "cockpit_display.h" #include "cockpit_display.c"

int main(void) {
uart1_init(BAUD_CALC(9600UL));

cd_set_rpm(789);
cd_set_speed(12);
cd_set_throttle(80);
cd_set_brake(60);

while (1) {
cd_set_blinker_left(true); _delay_ms(200);
cd_set_blinker_left(false); _delay_ms(200);

cd_set_light(LIGHT_PARKING); _delay_ms(700);
cd_set_light(LIGHT_LOW_BEAM); _delay_ms(700);
cd_set_light(LIGHT_HIGH_BEAM); _delay_ms(700);
}
}

### 3.8.3 Bibliothek Interface

#ifndef COCKPIT_DISPLAY_H

#define COCKPIT_DISPLAY_H

#include "usart.h"

#include <stdbool.h>

#include <stdint.h>

// these macros are used to choose between usart0 or usart1 #define CD_UART_PUTC uart0_putc
#define CD_UART_PUTS uart0_puts

typedef enum {
GEAR_NEUTRAL,
GEAR_FIRST,
GEAR_SECOND,
GEAR_THIRD,
GEAR_STATE_COUNT,
} GearState;

typedef enum {
LIGHT_OFF,
LIGHT_DAY,
LIGHT_LOW_BEAM,
LIGHT_HIGH_BEAM,
LIGHT_STATE_COUNT,
} LightState;

typedef enum {
BATTERY_EMPTY,
BATTERY_ONE_FOURTH,
BATTERY_TWO_FOURTH,
BATTERY_THREE_FOURTH,
BATTERY_FOUR_FOURTH,
BATTERY_CHARGING,
} BatteryState;

// Not implemented for now
// void cd_set_distance(uint8_t x);

void cd_set_blinker_left(bool enable); void cd_set_blinker_right(bool enable); void cd_set_warnblinker(bool enable); void cd_set_light(LightState light_state); void cd_set_rpm(uint16_t rpm);
/// @param speed_kmh range in [0; 99]
void cd_set_speed(uint8_t speed_kmh);
void cd_set_gear(GearState gear_state);
void cd_set_battery(BatteryState battery_state); /// @param percent range in [0; 100]
void cd_set_throttle(uint8_t percent);
/// @param percent range in [0; 100]
void cd_set_brake(uint8_t percent); #endif

## 3.9 Huppe


Da in meinem Pflichtenheft eine Hupe aufgelistet ist, muss diese auch eingebaut werden. Diese habe ich selber Bezahlt als kleine Entschädigung für das kaputte Display.

Abbildung 32: Miniatur Summer 24V (EMS-24L)

3.9.1 Erster Transistor

Abbildung 33: Kennlinien (Quelle: Datenblatt TIP120)

Als erstes würde ein TIP120 NPN in Erwegung gezogen, allerdings hat sich später herausgestellt das
er bei einem Strom von 3,5 A gekühlt werden muss.

Bei dem IRL3803 handelt es sich um einen Logik-Level-MOSFET, das heißt das er bei 5V fast vollständig durchschaltet. Für die Widerstände werden typische Werte genommen, wobei für R9 ein möglichst geringer Widerstand verwendet wird um ein PWM Signal zu ermöglichen. R10 dient als Pull-Down-Widerstand. R9 als Strom begrenzer, da ein MOSFET sich wie ein Kondensator am Gate verhält und zu Beginn eines Schaltzykluses viel Strom zieht.

Die Diode dient als Freilaufdiode, falls eine induktive Last angeschlossen wird.

## 3.10 Power-LED Dimensionierung

Schaltplanausschnitt 2: Power-LED

Die LED P1 zeigt an ob die Vcc Spannung mit 5V anliegt. Es handelt sich hier um eine grüne Low-
Power-LED mit sehr geringen Strom verbrauch.

Bei einer Status-LED sind 10% Schwankung des Stromes zu vernachlässigen.

## 3.11 Lenkrad

Die Taster werden im Lenkrad eingebaut. Der Start/Stop/Rückwärts Schalter legt den Vorwärts- bzw. Rückwärtsgang fest und sendet diese Information an den Antrieb weiter.

Abbildung 34: Lenkrad Taster

Abbildung 36: Taster-Anschluss

Abbildung 35: Start/Stop/Rückwärts

## 3.12 Cockpit-Platine

Als Erstes wurden alle benötigten Anschlüsse eingeplant, dann wurde daraus ein Schaltplan erstellt. Bei der Layout-Erstellung wurden die Anschlüsse als Erstes so positioniert wie sie real Sinn machen. Anschließend wurden die Leitungen verbunden.

Nach der ersten Version (Rev1) fiel auf das die Anschlüsse für die Taster besser oben anstatt von der Seite positioniert werden. Also wurde das Layout erneut erstellt und die aktuelle und finale Version (Rev2) ist entstanden.

Abbildung 37: Entwurf der Cockpitplatine (Rev1)


Abbildung 38: Schaltplan der Cockpitplatine Rev 2


Abbildung 39: Leiterbahnen (bottom) der Cockpitplatine Rev 2

Abbildung 40: Bauteilansicht (top) der Cockpitplatine Rev 2


Um die Abmessungen besser einschätzen zu können, wurde das Layout auf Papier in original Größe ausgedruckt.

Abbildung 41: Abmessung Ausdruck

### 3.12.1 Prüfprotokoll

Bedingung | geprüft von
Dean | Henry | Tammo

### 1. Schaltplan

Title ist sinnvoll. | x | x | x
Beschreibung ist verständlich. | x | x | x
Alle Bauteile sind korrekt bezeichnet. | x | x | x
Dimensionierung des Vorwiderstands der Power LED isr nachvollziehbar. | x | x | x
Dimensionierung des Widerstands für den Darlingtontransistor der Hupe ist nachvollziehbar. | x | x | x
Hupen Schaltung korrekt (MC Pin, Transistor und Diode). | x | x | x
Dimensionierung des Spannungsteiler für das Bluetooth-Modul ist nachvollziehbar. | x | x | x
Alle verwendeten Anschlüsse der AT90CAN32 Platine mit dem Schaltplan überprüft. | x | x | x
Alle Messbrücken sind passend beschriftet. | x | x | x
Alle verwendeten Anschlüsse der AT90CAN32 Platine nachgemessen | x
Anschlussstecker des Displays durch Messen überprüft. | x
Anschlussstecker der linken Tasterplatine durch Messen überprüft. | x
Anschlussstecker der rechte Tasterplatine durch Messen überprüft. | x

### 2. Platine

Jedes Bauteil ist montierbar. | x | x | x
Leitungen welche 4 Ampere Leiten haben 1,3 mm Breite und einen Abstand von 0,6 mm. | x | x | x
Restliche Leitungen haben eine Breite von 0,6 mm Breite und einen Abstand von 0,5 mm. | x | x | x
DRC (Design Rules Checker) wurde durchgeführt. | x | x | x
Platinen beschriftung wurde passend gewählt und ist gespiegelt. | x | x | x
Position der Ausgänge und der LED wurden passend gewählt. | x | x | x
Alle Footprints wurden nachgemessen. | x
Jedes Bauteil ist vorhanden. | x

Tabelle 7: Prüfprotokoll von der Cockpit-Platine

Nachdem die sehr häufig geprüfte Platine gedruckt wurde, fiel auf das der Mikrocontroller sich nicht programmieren lies. Relativ schnell war der Fehler klar, der MOSI bzw. MISO Anschluss des SPI ist nicht für ISP (In-System-Programming), stattdessen muss TXD0 und TXD1 verwendet werden. Dieser Fehler würde durch eine Brücke behoben. Alle gezeigten Schaltpläne in dieser Dokumentation haben die Brücke bereits eingezeichnet.

Abbildung 43: gefräste Kupferplatte

Abbildung 42: Bestückte Platine

## 3.13 Cockpit-Programm

Beim Programmieren wurde darauf geachtet das nach EVA-Prinzip gearbeitet wird. Das heißt das erst alles Eingelesen, verarbeitet und anschließend Ausgegeben wird. Außerdem wurden Variablennamen extra ausführlich gewählt und ersetzen so häufig Kommentare, wie es auch schon in den 1.3 Code Konventionen (S. 4) festgelegt wurde. Hier ist Beispielhaft die Hauptschleife des Cockpits, der gesamte Code ist ebenfalls verfügbar.
int main(void) {
init();
sei();

// test_display();

GearState prev_gear_state = gear_state; LightState prev_light_state = light_state; bool prev_blinker_left = false;
bool prev_horn = false;
bool prev_blinker_right = false;

while (true) {
// --- Einlesen ---
const bool blinker_left = blinker_left_live; const bool blinker_right = blinker_right_live; horn = GET(SW_WARNBLINKER_HORN);

if (GET(SW_MOTOR_START_LA)) {
if (GET(SW_MOTOR_REVERSE_LA)) {
motor_state = STOP;
} else {
motor_state = REVERSE;
}
} else {
if (GET(SW_MOTOR_REVERSE_LA)) { motor_state = FORWARD;
} else {
motor_state = STOP;
uart_puts("error: Vorwärts- und Rückwärtsfahren nicht gleichzeitig "
"möglich. Taster auf defekt überprüfen.\n"); }
}

// --- Verarbeiten ---
if (light_switch) {
light_switch = false;
light_state = (light_state + 1) % LIGHT_STATE_COUNT; }

if (gear_up) {
gear_up = false;

if (gear_state < GEAR_STATE_COUNT - 1) { gear_state++;

}
} else if (gear_down) {
gear_down = false;

if (gear_state > 0) {
gear_state--;
}
}

// --- Ausgeben ---
if (blinker_left != prev_blinker_left) { prev_blinker_left = blinker_left; cd_set_blinker_left(blinker_left);

if (blinker_left) {
SET(LED_BLINKER_LEFT);
} else {
RESET(LED_BLINKER_LEFT);
}
}

if (light_state != prev_light_state) { cd_set_light(light_state);
}

if (horn != prev_horn) {
if (horn) {
SET(LED_WARNBLINKER_HORN); SET(HORN_PWM);
} else {
RESET(LED_WARNBLINKER_HORN); RESET(HORN_PWM);
}
}

if (gear_state != prev_gear_state) { cd_set_gear(gear_state);
}

if (blinker_right != prev_blinker_right) { cd_set_blinker_right(blinker_right);

if (blinker_right) {
SET(LED_BLINKER_RIGHT);
} else {
RESET(LED_BLINKER_RIGHT);
}
}

// some button LEDs are set in the ISR for simplicity

if (light_state != prev_light_state ||
blinker_right != prev_blinker_right) {
can_t msg_blinker = {
.flags.rtr = false,

.flags.extended = true,
.length = 1,
};

uint8_t blinker_front_command = blinker_right << BLINKER_BIT;

switch (light_state) {
case LIGHT_OFF:
break;
case LIGHT_DAY:
blinker_front_command |= 1 << LOWER_LIGHT_BIT; break;
case LIGHT_LOW_BEAM:
blinker_front_command |=
1 << UPPER_WEAK_LIGHT_BIT | 1 << LOWER_LIGHT_BIT;
break;
case LIGHT_HIGH_BEAM:
blinker_front_command |=
1 << UPPER_FULL_LIGHT_BIT | 1 << LOWER_LIGHT_BIT;
break;
case LIGHT_STATE_COUNT:
break; // unreachable
}

uart1_puts("info: sende Befehl zu Blinker vorne rechts:"); uart1_puthex(blinker_front_command);
uart_putc('\n');

msg_blinker.id = CAN_ID_TX_BLINKER_FRONT_RIGHT; msg_blinker.data[0] = blinker_front_command, can_send_message(&msg_blinker);

uint8_t blinker_back_command = blinker_right << BLINKER_BIT;

uart1_puts("info: sende Befehl zu Blinker hinten rechts\n"); msg_blinker.id = CAN_ID_TX_BLINKER_BACK_RIGHT; msg_blinker.data[0] = blinker_back_command, can_send_message(&msg_blinker);
}

if (light_state != prev_light_state || blinker_left != prev_blinker_left) {
can_t msg_blinker = {
.flags.rtr = false,
.flags.extended = true,
.length = 1,
};

uint8_t blinker_front_command = blinker_left << BLINKER_BIT;

switch (light_state) {
case LIGHT_OFF:
break;
case LIGHT_DAY:
blinker_front_command |= 1 << LOWER_LIGHT_BIT;

break;
case LIGHT_LOW_BEAM:
blinker_front_command |=
1 << UPPER_WEAK_LIGHT_BIT | 1 << LOWER_LIGHT_BIT;
break;
case LIGHT_HIGH_BEAM:
blinker_front_command |=
1 << UPPER_FULL_LIGHT_BIT | 1 << LOWER_LIGHT_BIT;
break;
case LIGHT_STATE_COUNT:
break; // unreachable
}

uart1_puts("info: sende Befehl zu Blinker vorne rechts:"); uart1_puthex(blinker_front_command);
uart_putc('\n');

msg_blinker.id = CAN_ID_TX_BLINKER_FRONT_LEFT; msg_blinker.data[0] = blinker_front_command, can_send_message(&msg_blinker);

uint8_t blinker_back_command = blinker_left << BLINKER_BIT;

uart1_puts("info: sende Befehl zu Blinker hinten rechts\n"); msg_blinker.id = CAN_ID_TX_BLINKER_BACK_LEFT; msg_blinker.data[0] = blinker_back_command, can_send_message(&msg_blinker);
}

prev_gear_state = gear_state; prev_light_state = light_state; prev_horn = horn;
prev_blinker_right = blinker_right; }

emergency_loop:
goto emergency_loop;
}

## 4 Grundlagen

In diesem Kapitel werden die Grundlagen zur bedienung der Software erklärt. So das man dieses Projekt weiter entwickeln oder warten kann. Dabei richtet sich diese Anleitung an Linux-Nutzer, einige Programme sind ebenfalls für andere System wie Windows verfügbar.

## 4.1 Kompilieren und Hochladen

Benötigtes Paket:
- cmake
Als erstes müssen die USB-Rechte eingestellt werden.
$ sudo dmesg
usb 1-2: New USB device found, idVendor=16c0, idProduct=05dc usb 1-2: Product: USBasp
https://wiki.archlinux.org/title/Udev#Allowing_regular_users_to_use_devices
$ sudo -e /etc/udev/rules.d/71-usbasp.rules
SUBSYSTEMS=="usb", ATTRS{idVendor}=="16c0", ATTRS{idProduct} =="05dc", MODE="0660", TAG+="uaccess"
CMake und Make sind Werkzeuge, die den Bau von Programmen steuern, ähnlich wie eine IDE (Microchip Studio), nur über die Kommandozeile. CMake erzeugt Baupläne, die das System und den Compiler kennen, und Make führt diese Pläne aus, übersetzt den Code und erstellt die ausführbaren Dateien.

$ cmake -B build

Dieser Befehl erzeugt in einem neuen Verzeichnis namens „build“ alle notwendigen Dateien, die für den Bau des Projekts benötigt werden. CMake liest die „CMakeLists.txt“ Datei aus dem „src“ Verzeichnis, plant welche Dateien kompiliert werden müssen, und erstellt die Bauanweisungen (Makefile).

$ make

Make liest die von CMake erzeugten Makefiles und führt die Anweisungen aus. Es kompiliert die Quellcodes in Maschinencode und erstellt daraus die fertigen Programme oder Bibliotheken. Make sorgt dafür, dass nur die geänderten Dateien neu gebaut werden, was Zeit spart.

## 4.2 UART Übertragung

### 4.2.1 Text übertragen

Benötigtes Paket:
- minicom
1. USB-zu-Seriell-Konverter Geräte Schnittstelle finden (z. B. /dev/ttyUSB0 oder /dev/ttyACM0):

$ ls /dev/tty*

2. Serielle Übertragung öffnen. In diesem Fall mit dem Tool „minicom“ und eine BAUD-Rate von 9600 bps:
$ minicom -D /dev/ttyUSB0 -b 9600

### 4.2.2 Rohdaten übertragen

Um Binär oder Hexadezimal über UART zu senden kann man nicht minicom verwenden. In diesem Beispiel wird das Standard-Linux-Interface genutzt.

1. BAUD-Rate einstellen (z. B. 9600 bps):
$ stty -F /dev/ttyUSB0 9600
2. Nachricht senden (z. B. für das Cockpit-Display):
$ printf 'bL.pic=1\xFF\xFF\xFF' > /dev/ttyUSB0 Hierbei ist die Nachricht: „bL.pic=1“ und drei Mal FFh zum beenden des Befehls.

### 4.2.3 Bluetooth Übertragung

In diesem Kapitel wird erklärt wie man eine Verbindung mit dem Bluetooth-Modul (siehe 3.4 Bluetooth-Modul, S. 22) aufnehmen kann.

Warnung: IOS unterstützt keine Verbindung zu SPP (Serial Port Profile), sondern nur BLE (Bluetooth Low Energy). Da es sich hier um SPP handelt, ist keine Verbindung mit dem iPhone oder iPad möglich.

Benötigte Pakete:
- minicom
- bluez
- bluez-deprecated-tools
Die Arch Wik¹
hat eine ausführliche Erklärung wie man sich mit einem Bluetooth-Gerät verbindet.

Nachdem eine Bluetooth-Verbindung hergestellt wurde, muss sie einer device-Datei gebunden werden:

$ sudo rfcomm bind rfcomm0 <MAC Addresse des Bluetooth-Moduls>
Anschließend kann eine serielle Übertragung (siehe 4.2 UART Übertragung, S. 55) mit einer BAUD-Rate von 9600 bps hergestellt werden:
$ minicom -D /dev/rfcomm0 -b 9600
Das Blinken auf dem Bluetooth-Modul sollte aufhören und die Status-LED sollte konstant Leuchten.

1 mehr Informationen zu Bluetooth mit Linux in der Arch Wiki [AW01]

## 4.3 CAN Sniffing (PCAN-USB)

Benötigte Pakete:

- can-utils

Als CAN-Interface für USB wird der PCAN-USB IPEH-002021 von PEAK-System verwendet.

Der D-Sub stecker von allen Modulen ist nach CiA® 106 (siehe Abbildung 9: männlicher CAN D-Sub Anschluss nach CiA® 106 (Quelle: PCAN-USB Anleitung), S. 16)

### 4.3.1 Empfangen

Der folgende Befehl aktiviert das Netzwerk-Interface can0 als CAN-Bus-Schnittstelle und setzt dabei die Übertragungsrate auf 125 kbit/s. Dieser Schritt muss nur einmal durchgeführt werden.
$ sudo ip link set can0 up type can bitrate 125000
Anschließend können Nachrichten des CAN-Busses augegeben werden.
$ candump can0
Mögliche Ausgabe:
can0 400 [8] 01 02 02 03 04 05 06 07

### 4.3.2 Senden

Beispiel mit ID = 4AAh und erstes Datenbyte = 0Fh, zweites Datenbyte = 55h: $ cansend 4AA#0F55

### 4.3.3 Fehlerbehebung

Eventuell muss der Treiber von PEAK-System manuell installiert werden.

Ob ein Treiber installiert ist kann man zum Beispiel über die System-Logs herausfinden. Da der Treiber jenach Distrobution auch anders als peak_usb benannt sein kann, muss man eventuell den gesuchten Eintrag mit can0, pcan oder peak suchen.
$ sudo dmesg | grep -i peak_usb
Wenn die Ausgabe so ähnlich aussieht ist der Treiber installiert:
peak_usb 3-2:1.0: PEAK-System PCAN-USB adapter hwrev 28 serial peak_usb 3-2:1.0 can0: attached to PCAN-USB channel 0 usbcore: registered new interface driver peak_usb
Falls der Treiber nicht installiert ist kann man ihn über den Package-Manager des Systems herunterladen oder über die Webseite von PEAK-Systems.

Abbildung 44: PCAN-USB (Quelle: peak-system.com)

## 5 Fazit

## 5.1 Kosten

| Preis pro Stunde | Arbeitszeit (h) | Preis
Dokumentation | 15,00 € | 76 | 1.140,00 €
Entwicklungszeit | 25,00 € | 154 | 3.850,00 €
| gesamt | 230 | 4.990,00 €

Tabelle 8: Arbeitszeit Kosten

| Anzahl | Preis pro Stück | Preis
5x2 gewinkelte Buchse | 3 | 0,90 € | 2,70 €
3x2 gewinkelte Buchse | 1 | 0,80 € | 2,40 €
13x2 Buchse | 2 | 1,00 € | 2,00 €
Widerstände der E12-Reihe | 7 | 0,10 € | 0,70 €
Kupferplatte | 1 | 6,00 € | 6,00 €
Nextion Display | 1 | 95,00 € | 95,00 €
2-pol Anschluss | 1 | 1,10 € | 1,10 €
3-pol Anschluss | 1 | 1,20 € | 1,20 €
LED | 1 | 0,10 € | 0,10 €
| | gesamt | 111,20 €

Tabelle 9: Material Kosten

Die gesamten Kosten belaufen sich auf 5101,20 €.

## 5.2 Reflexion

Der Terminplan war von Anfang an sehr knapp bemessen und die zusätzlichen Hausaufgaben, welche uns an das Projekt führen sollten, haben mich zu mindestens sehr gebremst, da man jedes mal den Prozess dokumentieren musste. Ich hätte es besser gefunden hätten wir frei am Projekt arbeiten können. Die geplanten blauen Felder (siehe 7.2 Terminplan, S. 61) passen ziemlich gut den tatsächlichen Arbeitszeiten überein. Gerade mit dem Blick auf den Ergebnissen den vergangenen Jahren bin ich zufrieden mit meinen Beitrag zum Go-Kart. Alle Aufgaben aus dem Lasten- und Pflichtenheft wurden realisiert.

Wenn ich heute nochmal das Projekt beginnen würde, würde ich weniger Zeit mit den alten Dokumentation verbringen, diese haben mir oft nicht weiter geholfen und da man den Angaben nicht vertrauen konnte, musste hinterher fasst alles Ausgemessen werden.

Insbesondere die Teamarbeit hat meine Kompetenzen erweitert. Das Team war sehr engagiert und man konnte gut zusammen arbeiten.

## 5.3 Ausbau

Diese Themen sollten von dem Nachfolger bearbeitet werden:

1. Gehäuse für Cockpit mit 3D-Drucker erstellen.
2. Tasterplatinen für Lenkrad erneuern und die Kabelbrücken somit ersetzen.
3. Gehäuse für die Taster im Lenkrad erstellen.
4. Steuerprogramm für den PC um visuell auszuwerten und Befehle zu senden.
5. Restliche CAN-Nachrichten in das Cockpit-Programm hinzufügen

Dean Schneider (Auftragnehmer) & Datum

## 6 Eidesstattliche Erklärung

Hiermit versichere ich, dass ich die vorliegende Dokumentation selbstständig verfasst und keine anderen als die angegebenen Quellen und Hilfsmittel benutzt habe. Alle Stellen, die wörtlich oder sinngemäß aus veröffentlichten oder nicht veröffentlichten Schriften entnommen wurden, sind als solche kenntlich gemacht.

Ferner versichere ich, dass die vorliegende Arbeit noch nicht in einem anderen Prüfungsverfahren vorgelegen hat.

## 7 Anhang

## 7.1 Projekte der Vorgänger

Hiervon sind hauptsächlich JCS-BK_1025 (Schaltpläne für Lichtanlage), JCS-BK_1049 (Lichtanlage) und JCS-BK_1046 (Lenkradknöpfe, Cockpitdisplay) von Bedeutung.

60

Tabelle 10: alte Projekte

Jahr | Projektbezeichnung | Projektfunktion | Auftragnehmer
2023 | JCS-BK_1071_GO-KART Blinker_Lenkrad_Anzeige | Blinkerinbetriebnahme, Lenkradanbindung und die Visualisierung per PC/Laptop, mit CAN-BUS Anbindung, Basis ist JCS-BK_MS-063, JCS-BK_MS-123 | Elias Hahne
2021 | JCS-BK_1046_GO-KART Fahrzeugarmaturenbrett | MC basiertes Armaturenbrett ist zu fertigen und die Visualisierung per Tablet / Handy, Basis ist JCS-BK_MS-063, JCS-BK_MS-123 | Christian Barth
2021 | JCS-BK_1049_GO-KART Lichtanlage | Es sind Front- und Rückleuchten zu erstellen und die Blinker sollen Als Lauflicht ausgeführt werden, Basis ist JCS-BK_MS-060, JCS-BK_MS-130 | Robin Kraus
2020 | JCS-BK_1034_GO-KART Fahrzeugarmaturenbrett | MC basiertes Armaturenbrett ist zu fertigen und die Visualisierung per Tablet / Handy, Basis ist JCS-BK_MS-063, JCS-BK_MS-123 | Daniel Plempe
2020 | JCS-BK_1037_GO-KART Lichtanlage | Es sind Front- und Rückleuchten zu erstellen und die Blinker sollen Als Lauflicht ausgeführt werden, Basis ist JCS-BK_MS-060, JCS-BK_MS-130 | Daniel Briem
2019 | JCS-BK_1022_GO-KART Fahrzeugarmaturenbrett | MC basiertes Armaturenbrett ist zu fertigen und die Visualisierung per Tablet / Handy, Basis ist JCS-BK_MS-063, JCS-BK_MS-123 | Tim Stöhr
2019 | JCS-BK_1025_GO-KART Lichtanlage | Es sind Front- und Rückleuchten zu erstellen und die Blinker sollen Als Lauflicht ausgeführt werden, Basis ist JCS-BK_MS-060, JCS-BK_MS-130 | Christoph Waßmuth
2018 | JCS-BK_1005_GO-KART Fahrzeugarmaturenbrett | MC basiertes Armaturenbrett ist zu fertigen und die Visualisierung per Tablet / Handy, Basis ist JCS-BK_MS-063, JCS-BK_MS-123 | Lukas Guse
2018 | JCS-BK_1008_GO-KART Lichtanlage | Es sind Front- und Rückleuchten zu erstellen und die Blinker sollen Als Lauflicht ausgeführt werden, Basis ist JCS-BK_MS-060, JCS-BK_MS-130 | Luis Nolte
2017 | JCS-BK_MS-123_GO-KART Fahrzeugarmaturenbrett | MC basiertes Armaturenbrett ist zu fertigen und die Visualisierung per Tablet / Handy, Basis ist JCS-BK_MS-063 | Nils Kölle
2017 | JCS-BK_MS-130_GO-KART Lichtanlage | Es sind Front- und Rückleuchten zu erstellen und die Blinker sollen Als Lauflicht ausgeführt werden, Basis ist JCS-BK_MS-060 | Johannes Wachs
| JCS-BK_MS-060_GO-KART Lichtanlage | Front- und Rückleuchten sind zu fertigen | Philipp Junge, Jan Schmidt
| JCS-BK_MS-063_GO-KART Fahrzeugarmaturenbrett | JAVA-Tablet und MC Armaturenbrett ist zu fertigen | Patrick Schwarz

## 7.2 Terminplan

Projekt – Thema; 1. Woche / KW 36; 2. Woche / KW 37; 3. Woche / KW 38; 4. Woche / KW 39; 5. Woche / KW 40; 6. Woche / KW 41; 7. Woche / KW42; Aktion; Dokumentation; Projektstart; Arbeitsunfähig; Pflichtenheft mind. 10 Seiten; Überarbeitet Pflichtenheft mind. 10 Seiten; Ferien; Bestandsaufnahme; Licht; Bluetooth-Anbindung; CAN-Bus-Anbindung; Lenkrad; Cockpitdisplay / Statusdisplay; Masterplatine Bearbeitung; Platine für Cockpit; Grundlagen (z.B. I2C); Präsentation; Abnahme/Präsentation; 0 Legende; Projektwoche; Abgabe; Zwischenkontrolle; Bearbeitung; Prüfungsphase; Reale Zeiten

61

Tabelle 11: Terminplan 01.09. - 19.09.2025

2. | Pflichtenheft/Terminplan | 24 | 2 | 4,5 | 1,5 | 3 | 10 | 3

Projekt – Thema; 8. Woche / KW 43; 9. Woche / KW 44; 10. Woche / KW 45; 11. Woche / KW 46; 12. Woche / KW 47; 13. Woche / KW 48; 14. Woche / KW 49; Aktion; Dokumentation; Ferien; Arbeitsunfähig; Projektwoche; Draft 1 30% der Dokumentationsabgabe; Software Zwischenabgabe; Pflichtenheft/Terminplan; Bestandsaufnahme; Licht; Bluetooth-Anbindung; CAN-Bus-Anbindung; Lenkrad; Masterplatine Bearbeitung; Platine für Cockpit; Präsentation; Abnahme/Präsentation; 0 Legende; Abgabe; Zwischenkontrolle; Bearbeitung; Prüfungsphase; Reale Zeiten

62

Tabelle 12: Terminplan 20.10. - 07.12.2025

8. | Cockpitdisplay / Statusdisplay | 27 | 5 | 3
11. | Grundlagen (z.B. I2C) | 17 | 1.5 | 1.5 | 6 | 6 | 3

Projekt – Thema; 15. Woche / KW 50; 16. Woche / KW 51; 17. Woche / KW 52; 18. Woche / KW 01; 19. Woche / KW 02; 20. Woche / KW 03; Aktion; Dokumentation; Ferien; Software Zwischenabgabe; Draft 2 80% der Dokumentationsabgabe; Noteneintragung; Pflichtenheft/Terminplan; Bestandsaufnahme; Licht; Bluetooth-Anbindung; CAN-Bus-Anbindung; Lenkrad; Masterplatine Bearbeitung; Platine für Cockpit; Grundlagen (z.B. I2C); Präsentation; Abnahme/Präsentation; 0 Legende; Projektwoche; Abgabe; Zwischenkontrolle; Bearbeitung; Prüfungsphase; Reale Zeiten; Projektwoche 21. Woche / KW 04

63

Tabelle 13: Terminplan 08.12.2025 - 25.01.2026

8. | Cockpitdisplay / Statusdisplay | 27 | 1 | 1,5 | 3 | 1

Projekt – Thema; 22. Woche / KW 05; 23. Woche / KW 06; 24. Woche / KW 07; 25. Woche / KW 08; 26. Woche / KW 09; 27. Woche / KW 10; 28. Woche / KW 11; Aktion; Dokumentation; Zeugnisausgabe; Projektwoche; Präsentationsabgabe TdoT; Tag der offenen Tür; Klassenfahrt; Dokumentationsabgabe; Pflichtenheft/Terminplan; Tag des Sports; Bestandsaufnahme; Licht; Bluetooth-Anbindung; CAN-Bus-Anbindung; Lenkrad; Masterplatine Bearbeitung; Platine für Cockpit; Grundlagen (z.B. I2C); Präsentation; Abnahme/Präsentation; 0 Legende; Abgabe; Zwischenkontrolle; Bearbeitung; Prüfungsphase; Reale Zeiten

64

Tabelle 14: Terminplan 26.01. - 15.03.2026

8. | Cockpitdisplay / Statusdisplay | 27 | 2,5 | 7 | 3

## 7.3 Meilensteine

Start-datum | Ziel-datum | Zeit (h) | Thema (Aufgabe)
01.09.25 | 11.09.25 | | Festlegen des Themas und der Projektteams (Informationssammlung, Pflichtenheft zur Aufgabenfixierung, Aufgabenverteilung im Team und Anfertigung des Detailterminplans)
12.09.25 | 08.10.25 | 18 | Abgabe des Pflichtenhefts
08.10.25 | 30.11.25 | 34 | Schaltplanerstellung / Programmierung von Modulen / Testaufbau / Modultests
08.10.25 | 30.11.25 | 11 | Abgabe der Draft 1 - Dokumentationsentwurf
31.11.25 | 23.01.26 | 5 | Statusermittlung / Terminplanprüfung
31.11.25 | 23.01.26 | 7 | Schaltplan- und Layouterstellung / Programmierung von Modulen Testaufbau / Modultests / Dokumentation
31.11.25 | 23.01.26 | 15 | Programmtests, Dokumentation, Fehleranalyse, Fehlerbeseitigung
31.11.25 | 23.01.26 | 20 | Abgabe der Draft2-Dokumentation 7:35 keine Verlängerung
23.01.26 | 13.03.26 | 85 | Programmtests, Dokumentation, Fehleranalyse, Fehlerbeseitigung
08.02.26 | 25.02.26 | 2 | Präsentation der Ergebnisse als Impress-Vortrag
12.02.26 | 13.02.26 | 15 | Präsentation der Zwischenstände am Tag der offenen Tür
10.03.26 | 13.03.26 | 10 | Abgabe des Projekts mit Abschluss-Dokumentation 24:00
16.03.26 | 20.03.26 | | Leistungsüberprüfung / Produktabnahme

Tabelle 15: Meilensteine

## 7.4 Tagesziele

Tabelle 16: Tagesziele Teil 1

Nr. | Datum | Zeit (h) | Tagesziel | Reflexion
1 | 2025-09-12 | 2,0 | Pflichtenheft Layout erstellen | Deckblatt und ungefähres Design fertig. Titelbild muss eingefügt werden.
2 | 2025-09-22 | 4,5 | Nach Erkältung an Pflichtenheft weiterarbeiten. | - Lastenheft eingefügt - Projekte der Vorgänger herausgesucht - Bereits vorhandene Elemente und meine Aufgaben herausgeschrieben
3 | 2025-09-25 | 1.5 | Pflichtenheft fortführen, insbesondere alle vorgegeben Tabellen einfügen (Meilensteine, Terminplan, …) | Terminplan eingefügt
4 | 2025-09-26 | 3,0 | Pflichtenheft weiter ausformulieren. | 50 Prozent
5 | 2025-09-27 | 4,0 | Pflichtenheft Aufgabenstellung definieren. Eventuell Zeitplan anpassen. | Aufgabenstellung weiter definiert und die letzten drei Vorgänger-Projekte analysiert.
6 | 2025-09-28 | 6,0 | Pflichtenheft erste Version | Erste Version fertiggestellt.
7 | 2025-10-08 | 3,0 | Pflichtenheft korrigieren. | Erfolgreich
8 | 2025-11-06 | 1,5 | Kegelbahn-Anzeige ansteuern | Schaltplan analysiert, Anschlüsse festgestellt
9 | 2025-11-07 | 1,5 | - Kegelbahn-Anzeige ansteuern - OLED Display ansteuern | Erfolgreich angesteuert
10 | 2025-11-08 | 3,0 | Bluetooth Modul ansteuern | Kann mit USB angesteuert werden.
11 | 2025-11-09 | 6,0 | Bluetooth Modul ansteuern | Kann vollständig angesteuert werden und vollständig dokumentiert.
12 | 2025-11-10 | 6,0 | Display testen und ansteuern | Das Display wurde mit 14V gebraten. Ich habe ein Ersatzdisplay bekommen. Allerdings habe ich heute größtenteils den anderen geholfen und bin daher nicht weiter gekommen.
13 | 2025-11-11 | 6,0 | Hausaufgaben zu den Kegelbahnanzeigen bearbeiten | Punkteanzeige fertig
14 | 2025-11-12 | 6,0 | Wurfanzeige für die Kegelbahn | Muss nur noch hochgeladen werden.
15 | 2025-11-13 | 6,0 | - Hausaufgabe zur Kegelbahn fertigstellen - kaputtes Display messen - AT90CAN Platine analysieren | - Hausaufgabe fertig - AT90CAN Platine wurde analysiert, allerdings funktioniert Hochladen aufgrund von avrdude noch nicht. Ich muss noch Feststellen, welchen Typ der Programmierer hat. - kaputtes Display messe ich zu Hause
16 | 2025-11-27 bis 2025-11-29 | 6,0 | Hausaufgabe TI_85_Arduino_CAN-BUS_Test nachholen. Testaufbau für CAN-Bus mit dem MCP2515 Modul. | Ich brauche ein zweites MCP2515 (und TJA1050) Modul um einen richtigen Test durchführen zu können. Ich kann also erst in der Schule weiterarbeiten.
17 | 03.12.25 | 4,0 | OLED Display ansteuern | Funktioniert mit Bibliothek. Außerdem Datenblatt analysiert, um die Einstellungen zu verstehen und eventuell selbst die Befehle zu senden.
18 | 05.12.25 | 1,5 | CAN Bus Test: Senden und Empfangen | CAN Bus Analyzer (PCAN) mit Software zum laufen bringen. Nicht abgeschlossen
19 | 05.12.25 | 3,0 | CAN Bus Test: Senden und Empfangen | Senden und Empfangen über ein CAN USB Interface funktioniert
20 | 12.12.25 | 3,0 | OLED Display ansteuern | An PWM und ADC gearbeitet
21 | 19.12.25 | 3,0 | CAN-Bus senden | OLED-Display, PWM, Analog mit C fertig SPI funktioniert nicht mit ATmega328p
22 | 08.01.26 | 1,5 | CAN-Bus-Nachricht senden | CAN-Bus-Nachricht senden und empfangen funktioniert.
23 | 09.01.26 | 5,0 | CAN Nachrichten auf OLED anzeigen. | Erfolgreich. Die Nachrichten werden fortlaufend angezeigt.
24 | 15.01.26 | 1,5 | Nextion Display ansteuern. | Das Nextion Display mit UART ansteuern und mit den anderen Bluetooth getestet.
25 | 16.01.26 | 3,0 | Cockpit Display angesteuert | Programm zum Ansteuern geschrieben
26 | 19.01.26 | 3,0 | Programm testen und Dokumentation schreiben über CAN-Bus, Display und Cockpit-Display. | Programm getestet

Tabelle 17: Tagesziele Teil 2

Nr. | Datum | Zeit (h) | Tagesziel | Reflexion
27 | 20.01.26 | 3,0 | Dokumentation schreiben über CAN-Bus, Display und Cockpit-Display. | Schaltplan für Bluetooth, cmake Erklärung, CAN-Sniffing
28 | 22.01.26 | 3,0 | Blinker Modul ansteuern | Blinker Modul muss neu programmiert werden, da das letzte Projekt (JCS-BK_1071) den Microcontroller mit einen Testprogramm programmiert hat. CAN-Bus-Steuerung
29 | 22.01.26 | 4,0 | Dokumentation weiter schreiben | allgemeine Verbesserungen Cockpit-Display Kapitel erste Version OLED-Display Kapitel erste Version
30 | 23.01.26 | 7,0 | Blinker Mikrocontroller testen Dokumentation Draft 2 | Blinker LEDs getestet, als Nächstes muss das Programm zum Steuern über CAN-Bus erstellt werden. Draft 2 fertiggestellt
31 | 24.01.26 | 4,0 | LEDs des Blinkers testen | Erfolgreich, allerdings scheint der MCU langsam nicht mehr programmierbar zu sein, es kommt häufig zu Fehlern beim hochladen.
32 | 27.01.26 | 3,0 | AT90CAN mit USART1 und USART0 gleichzeitig | Abgebrochen
33 | 28.01.26 | 2,5 | Cockpit Display testen mit Testprogramm und AT90CAN32. | Erfolgreich, es gab einen Bug in der Bibliothek für den AT90CAN32.
34 | 29.01.26 | 5,0 | ATmega16M1 programmieren und schließlich CAN-Bus für die Blinker testen. | Dokumentation besprochen und USB Rechte eingestellt. Das Problem mit dem Programmierer und ATmega16M1 lag, daran das 3.3V anstelle von 5V eingestellt waren. Als Erstes wird der AT90CAN mit CAN-Bus getestet.
35 | 30.01.26 | 3,0 | CAN-Bus mit AT90CAN32. | CAN-Bus-Test erfolgreich mit Dokumentation.
36 | 31.01.26 | 4,0 | CAN-Bus mit ATmega16M1 | Bug in der Bibliothek nicht gefunden allerdings eingekreist in der Interrupt routine (Er tritt nur auf wenn man Interrupts aktiviert).
37 | 01.02.26 | 7,0 | CAN-Bus mit ATmega16M1 Blinker Steuerung | Nach weiteren 3 Stunden endlich den Bug in der Bibliothek gefunden. Mithilfe ISR(BADISR_vect) trat der Reset nicht mehr auf. Dadurch konnte ich den Reset auf die ISR(CANIT_vect) zurückführen. Nach genauer Recherche im Datenblatt erkannte ich das CANIT_vect nicht für den ATmega16M1 geeignet ist, sondern nur CAN_INT_vect. Durch einfaches Austauschen war der Bug behoben. Blinker Steuerung fertig nach den internationalen Normen und Dokumentation geschrieben.
38 | 04.02.26 | 2,0 | UART für ATmega16M1 und steuerung des Blinkers über UART oder CAN-Bus. | Fertig, muss nur noch getestet werden.
39 | 09.02.26 | 6.5 | Blinker UART testen mit Bluetooth Modul. | Erfolgreich Zusätzlich: Statusnachricht im Intervall senden, PWM für Rücklicht, beides muss getestet werden
40 | 10.02.26 | 4,0 | neue Funktionen Testen Taster und Display planen, Display Bibliothek überarbeiten | Blinker Modul mit PWM morgen: CAN ID Tabelle, Taster und Display Platine
41 | 11.02.26 | 4,0 | CAN ID Tabelle, Taster und Display Platine erstellen | CAN-ID Tabelle erste Version. Den anderen geholfen.
42 | 12.02.26 | 7,0 | Tasterplatine Schaltung | Tasterplatine wird nicht erneuert. Verbindungsplatine Schaltung angefangen.
43 | 13.02.26 | 7,0 | Tasterplatinen ausmessen | Schaltplan fertiggestellt
44 | 14.02.26 | 4,0 | Testprogram für Cockpit erstellen | Erfolgreich
45 | 15.02.26 | 3,0 | Platinenplan angefangen | etwa 50%
46 | 16.02.26 | 7,0 | Platine fertigstellen | Erfolgreich. Prüfprotokoll wird in den nächsten Tagen von Henry und Tammo kontrolliert.
47 | 01.03.26 | 6,0 | Anschlüsse auf der Platine besser positionieren. | Erfolgreich
48 | 02.03.26 | 4,0 | Platine drucken und bestücken. | Gelötet und grundsätzlich getestet. Ein 5x2 wurde noch offen gelassen, bis klar ist ob noch ein besserer gewinkelter verfügbar ist.
49 | 04.03.26 | 2,0 | Programmieranschluss funktioniert nicht. | Warum ist MOSI an RXD0 angeschlossen?

Tabelle 18: Tagesziele Teil 3

Nr. | Datum | Zeit (h) | Tagesziel | Reflexion
49 | 04.03.26 | 2,0 | Programmieranschluss funktioniert nicht. | Warum ist MOSI an RXD0 angeschlossen?
50 | 05.03.26 | 5,0 | Platine reparieren und testen. | MOSI und RXD0 bzw. MISO und TXD0 mit einer Brücke verbunden. Hupe mit Testprogram getestet. Pull-down-Widerstand eines Tasters war nicht eingebaut. Alle Taster und Bluetooth getestet, somit ist die gesamte Hardware getestet. Programm für Cockpit fertiggestellt. CAN-Bus-Kommunikation mit anderen Projekten ist noch offen.
51 | 07.03.26 | 5,0 | Dokumentation überarbeiten | Abstract, Platine erklärt, Rechnungen überarbeitet und generelle Verbesserungen
52 | 10.03.26 | 3,0 | Besprochene Änderungen in Dokumentation anpassen und Signalzeitdiagramm erstellen. | Signalzeitdiagramm erstellt
53 | 12.03.26 | 3,0 | Dokumentation überarbeiten | zusätzlich noch Programm auf Blinker gespielt. Ein Blinker ist angepasst.
54 | 13.03.26 | 5,0 | Dokumentation überarbeiten | Erfolgreich
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

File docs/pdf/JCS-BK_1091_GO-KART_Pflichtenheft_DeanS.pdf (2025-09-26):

## BERUFLICHES GYMNASIUM TECHNIK

JOHANN-CONRAD-SCHLAUN-BERUFSKOLLEG

[Titel Bild]

Pflichtenheft

Go-Kart
Blinker Lenkrad Anzeige

Dean Schneider

Projektleitung: | Michael Schmidt
Projektnummer: | JCS-BK_1091_GO-KART
Jahrgang: | GYT26
Fach: | Projekt mit Elektrotechnik und Informatik
Verfasser: | Dean Peter Schneider
E-Mail: | dean@kowatsch.de
Projektstart: | 1. September 2025
Projektende: | 20. März 2026
Letzte Änderung: | 22. September 2025

Inhaltsverzeichnis

### 1 Einleitung

Was beschreibt dieses Dokument?

### 2 Aufgabenstellung

Zweck und Ziel

### 3 Ablauforganisation

### 3.1 Meilensteine

1

### 3.2 Terminplan

2

3

### 4 Auftragsbestätigung

### 5 Anhang

### 5.1 Lastenheft

4


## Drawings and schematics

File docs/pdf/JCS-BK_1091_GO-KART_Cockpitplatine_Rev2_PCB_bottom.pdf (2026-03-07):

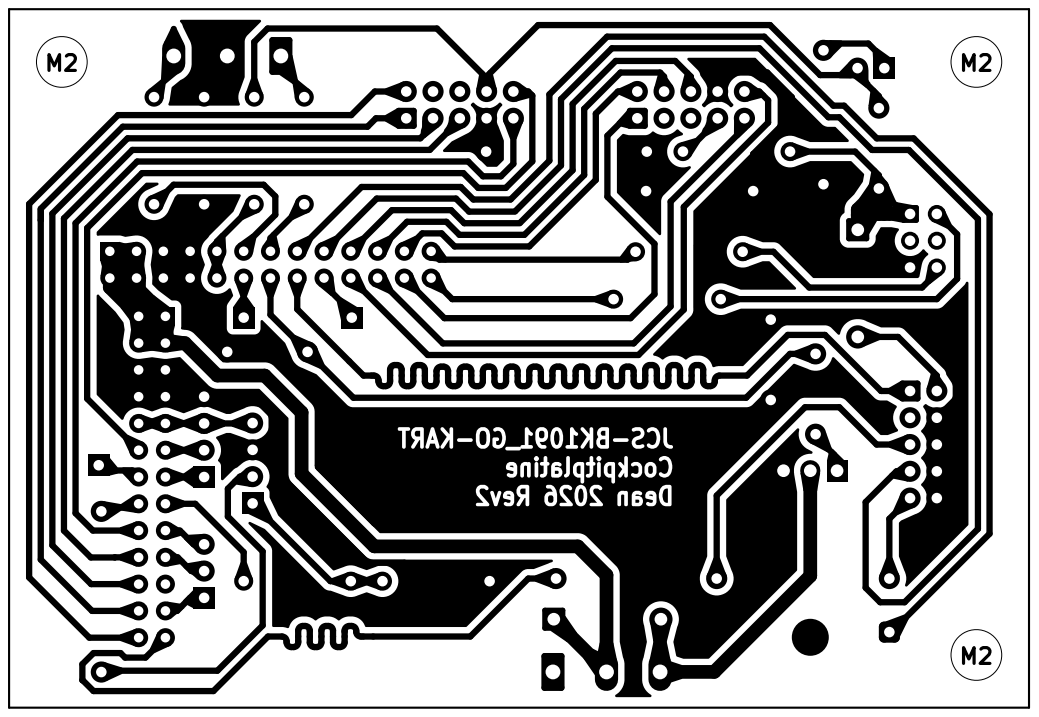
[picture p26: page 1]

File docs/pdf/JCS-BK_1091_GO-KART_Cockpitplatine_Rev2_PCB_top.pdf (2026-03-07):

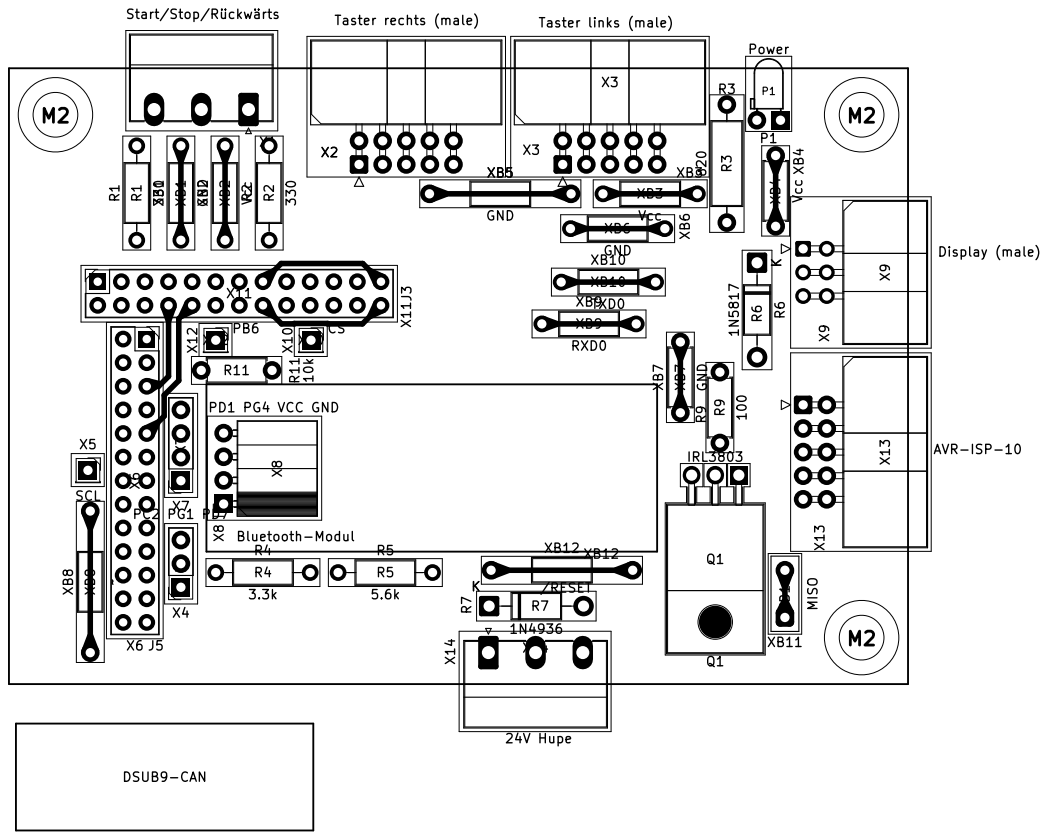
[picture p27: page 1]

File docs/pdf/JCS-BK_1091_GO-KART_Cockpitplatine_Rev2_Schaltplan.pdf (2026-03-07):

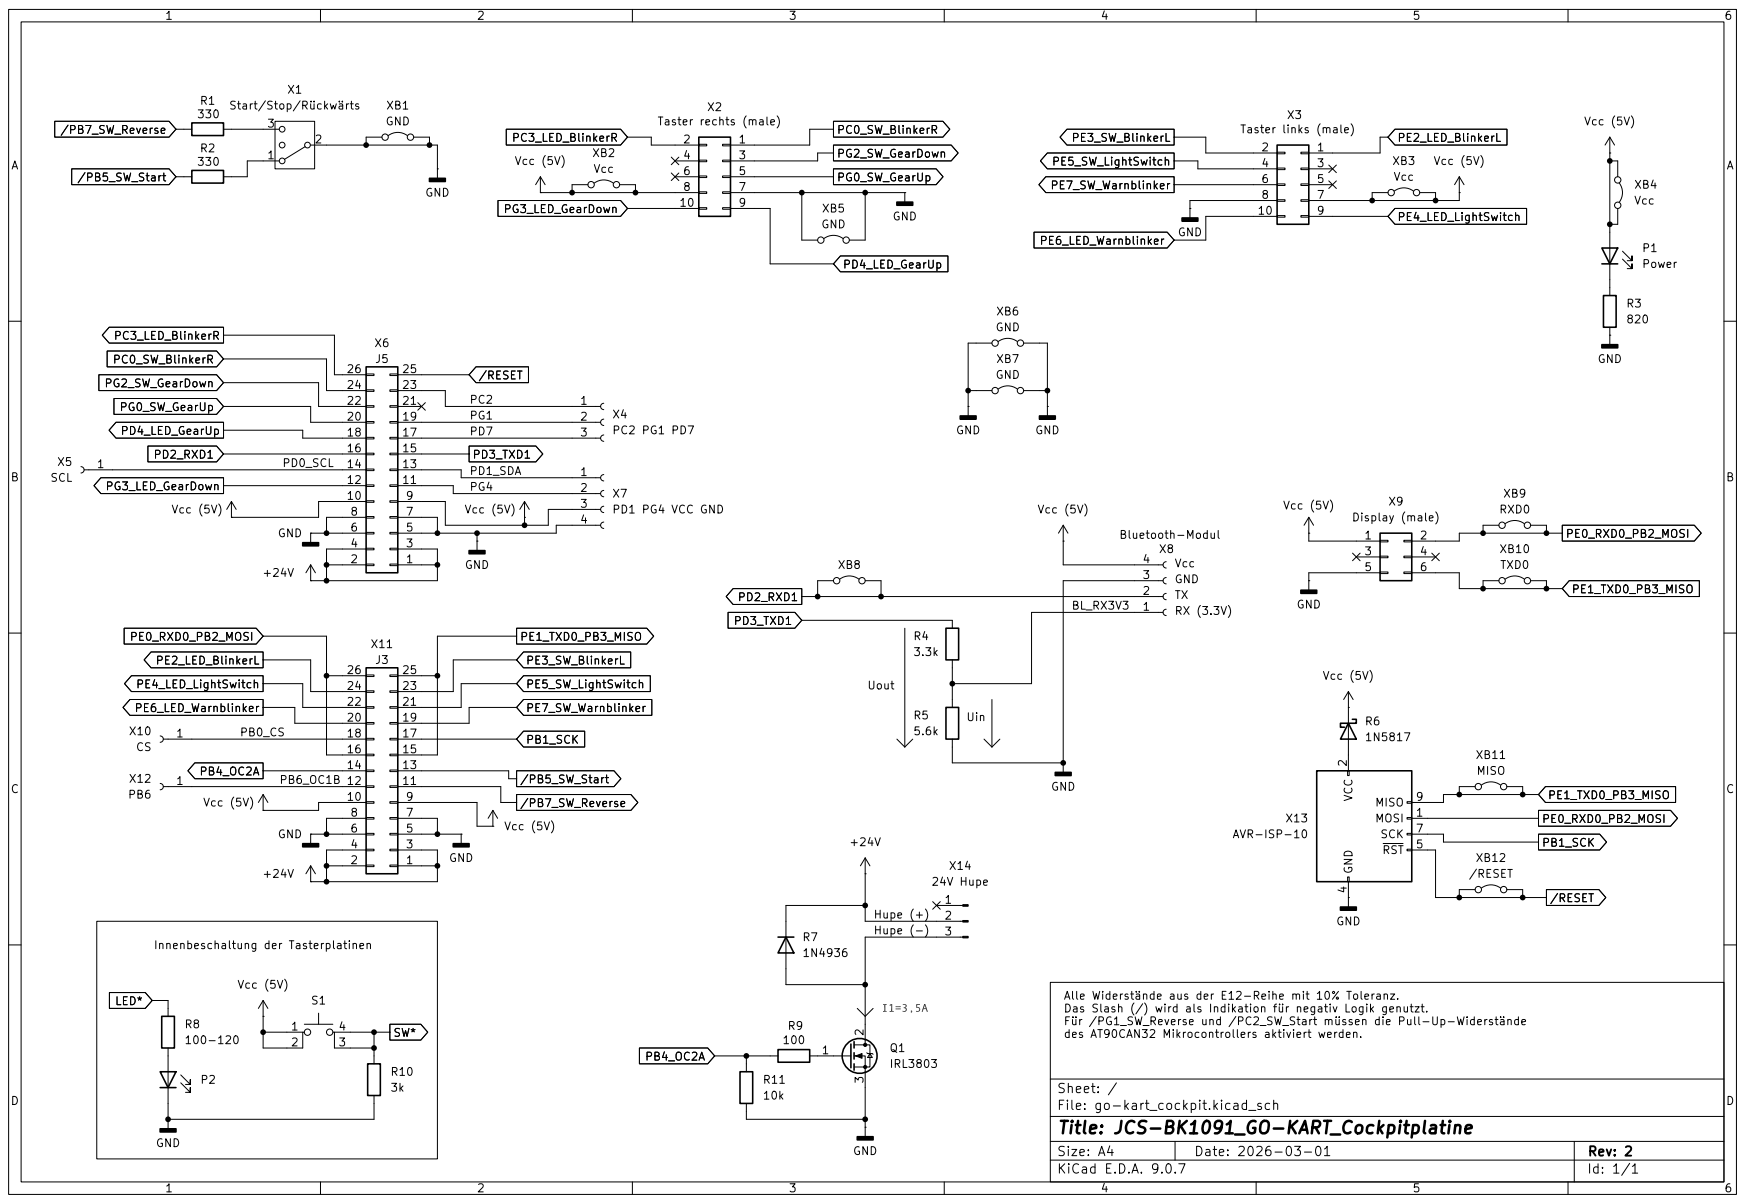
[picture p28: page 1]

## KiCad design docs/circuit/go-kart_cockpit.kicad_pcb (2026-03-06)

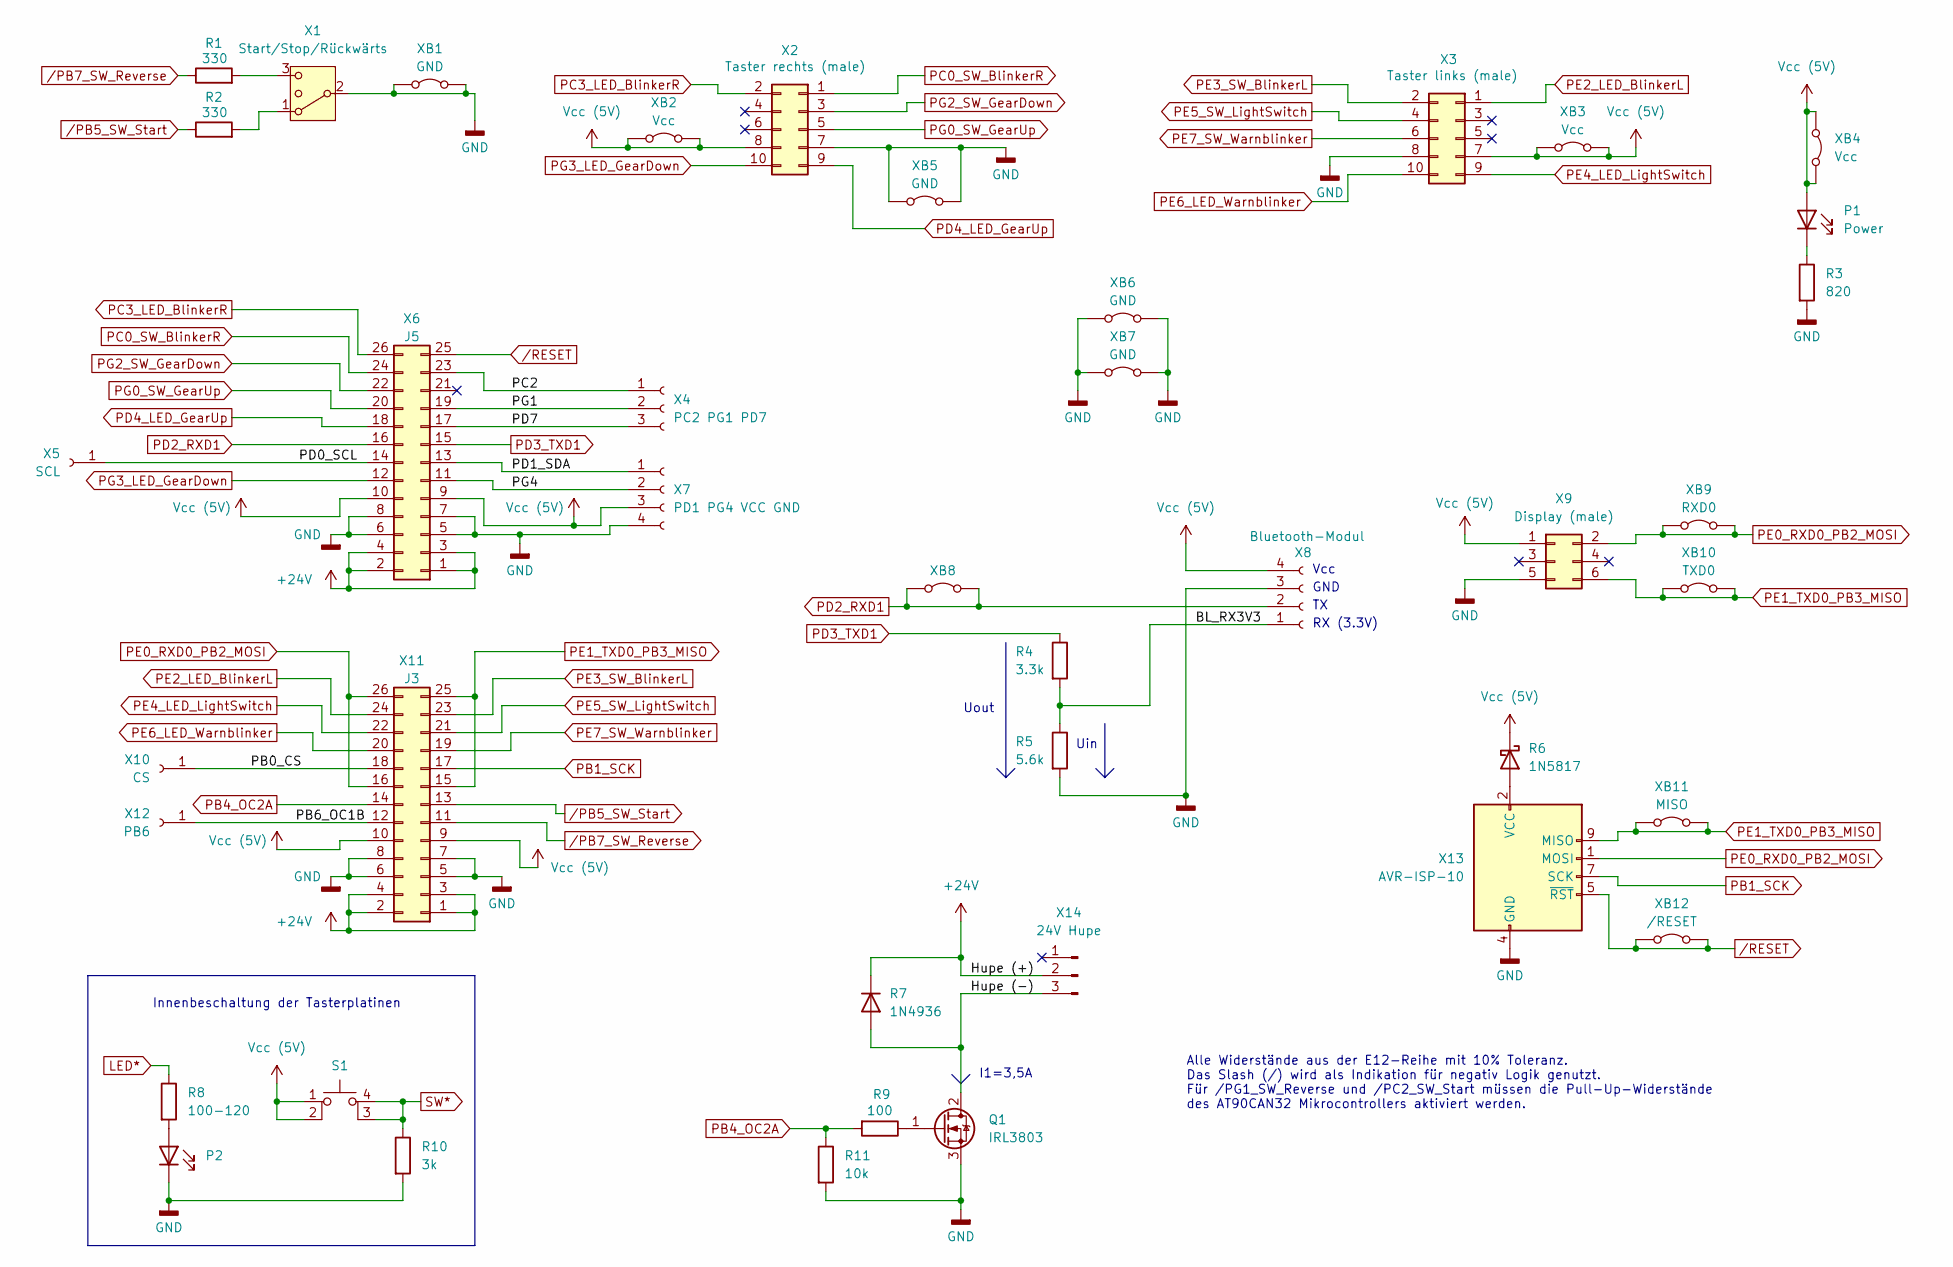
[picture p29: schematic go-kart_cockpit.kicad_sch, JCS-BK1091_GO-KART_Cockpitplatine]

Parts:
P1, P2: Power; LED_D3.0mm_Horizontal_O1.27mm_Z6.0mm
Q1: IRL3803; TO-220F-3_Horizontal_TabDown
R1, R2: 330; R_Axial_DIN0207_L6.3mm_D2.5mm_P10.16mm_Horizontal
R3: 820; R_Axial_DIN0309_L9.0mm_D3.2mm_P12.70mm_Horizontal
R4: 3.3k; R_Axial_DIN0207_L6.3mm_D2.5mm_P10.16mm_Horizontal
R5: 5.6k; R_Axial_DIN0207_L6.3mm_D2.5mm_P10.16mm_Horizontal
R6: 1N5817; D_DO-41_SOD81_P10.16mm_Horizontal
R7: 1N4936; D_DO-41_SOD81_P10.16mm_Horizontal
R8: 100-120
R9: 100; R_Axial_DIN0207_L6.3mm_D2.5mm_P7.62mm_Horizontal
R10: 3k
R11: 10k; R_Axial_DIN0207_L6.3mm_D2.5mm_P7.62mm_Horizontal
S1: SW_MEC_5E
X1: Start/Stop/Rückwärts; PhoenixContact_MC_1,5_3-G-5.08_1x03_P5.08mm_Horizontal
X2: Taster rechts (male); IDC-Header_2x05_P2.54mm_Horizontal
X3: Taster links (male); IDC-Header_2x05_P2.54mm_Horizontal
X4: PC2 PG1 PD7; PinSocket_1x03_P2.54mm_Vertical
X5: SCL; PinSocket_1x01_P2.54mm_Vertical
X6: J5; PinSocket_2x13_P2.54mm_Vertical
X7: PD1 PG4 VCC GND; PinSocket_1x04_P2.54mm_Vertical
X8: Bluetooth-Modul; PinSocket_1x04_P2.54mm_Horizontal
X9: Display (male); IDC-Header_2x03_P2.54mm_Horizontal
X10: CS; PinSocket_1x01_P2.54mm_Vertical
X11: J3; PinSocket_2x13_P2.54mm_Vertical
X12: PB6; PinSocket_1x01_P2.54mm_Vertical
X13: AVR-ISP-10; IDC-Header_2x05_P2.54mm_Horizontal
X14: 24V Hupe; PhoenixContact_MC_1,5_3-G-5.08_1x03_P5.08mm_Horizontal
XB1, XB6: GND; R_Axial_DIN0207_L6.3mm_D2.5mm_P10.16mm_Horizontal
XB2, XB3: Vcc; R_Axial_DIN0207_L6.3mm_D2.5mm_P10.16mm_Horizontal
XB4: Vcc; R_Axial_DIN0207_L6.3mm_D2.5mm_P7.62mm_Horizontal
XB5: GND; R_Axial_DIN0207_L6.3mm_D2.5mm_P15.24mm_Horizontal
XB7: GND; R_Axial_DIN0207_L6.3mm_D2.5mm_P7.62mm_Horizontal
XB8: R_Axial_DIN0207_L6.3mm_D2.5mm_P15.24mm_Horizontal
XB9: RXD0; R_Axial_DIN0207_L6.3mm_D2.5mm_P10.16mm_Horizontal
XB10: TXD0; R_Axial_DIN0207_L6.3mm_D2.5mm_P10.16mm_Horizontal
XB11: MISO; TestPoint_2Pads_Pitch5.08mm_Drill1.3mm
XB12: /RESET; R_Axial_DIN0207_L6.3mm_D2.5mm_P15.24mm_Horizontal

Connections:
+24V: R7.1 (K), X6.1, X6.2, X6.3, X6.4, X11.1, X11.2, X11.3, X11.4, X14.2
/BL_RX3V3: R4.2, R5.1, X8.1
/Hupe (-): Q1.2 (D), R7.2 (A), X14.3
/PB0_CS: X10.1, X11.18
/PB6_OC1B: X11.12, X12.1
/PC2: X4.1, X6.23
/PD0_SCL: X5.1, X6.14
/PD1_SDA: X6.13, X7.1
/PD7: X4.3, X6.17
/PG1: X4.2, X6.19
/PG4: X6.11, X7.2
GND: P2.1 (K), Q1.3 (S), R3.2, R5.2, R10.2, R11.2, X1.2 (3), X2.7, X3.8, X6.5, X6.6, X6.7, X6.8, X7.4, X8.3, X9.5, X11.5, X11.6, X11.7, X11.8, X13.4 (GND), X13.6 (GND), X13.8 (GND), X13.10 (GND), XB1.1 (A), XB1.2 (B), XB5.1 (A), XB5.2 (B), XB6.1 (A), XB6.2 (B), XB7.1 (A), XB7.2 (B)
unnamed: P1.1 (K), R3.1
unnamed: P2.2 (A), R8.2
unnamed: Q1.1 (G), R9.1
unnamed: R2.2, X1.1
unnamed: R6.2 (A), X13.2 (VCC)
unnamed: R10.1, S1.3 (K), S1.4 (A)
unnamed: R1.2, X1.3 (4)
PB1_SCK: X11.17, X13.7 (SCK)
PB4_OC2A: R9.2, R11.1, X11.14
PC0_SW_BlinkerR: X2.1, X6.24
PC3_LED_BlinkerR: X2.2, X6.26
PD2_RXD1: X6.16, X8.2, XB8.1 (A), XB8.2 (B)
PD3_TXD1: R4.1, X6.15
PD4_LED_GearUp: X2.9, X6.18
PE0_RXD0_PB2_MOSI: X9.2, X11.16, X11.26, X13.1 (MOSI), XB9.1 (A), XB9.2 (B)
PE1_TXD0_PB3_MISO: X9.6, X11.15, X11.25, X13.9 (MISO), XB10.1 (A), XB10.2 (B), XB11.1 (A), XB11.2 (B)
PE2_LED_BlinkerL: X3.1, X11.24
PE3_SW_BlinkerL: X3.2, X11.23
PE4_LED_LightSwitch: X3.9, X11.22
PE5_SW_LightSwitch: X3.4, X11.21
PE6_LED_Warnblinker: X3.10, X11.20
PE7_SW_Warnblinker: X3.6, X11.19
PG0_SW_GearUp: X2.5, X6.20
PG2_SW_GearDown: X2.3, X6.22
PG3_LED_GearDown: X2.10, X6.12
Vcc (5V): P1.2 (A), R6.1 (K), S1.1, S1.2, X2.8, X3.7, X6.9, X6.10, X7.3, X8.4, X9.1, X11.9, X11.10, XB2.1 (A), XB2.2 (B), XB3.1 (A), XB3.2 (B), XB4.1 (A), XB4.2 (B)
/PB5_SW_Start: R2.1, X11.13
/PB7_SW_Reverse: R1.1, X11.11
/RESET: X6.25, X13.5 (~RST), XB12.1 (A), XB12.2 (B)

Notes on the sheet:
Innenbeschaltung der Tasterplatinen
Uin
Alle Widerstände aus der E12-Reihe mit 10% Toleranz. Das Slash (/) wird als Indikation für negativ Logik genutzt. Für /PG1_SW_Reverse und /PC2_SW_Start müssen die Pull-Up-Widerstände des AT90CAN32 Mikrocontrollers aktiviert werden.
I1=3,5A
GND
Vcc
Uout
RX (3.3V)

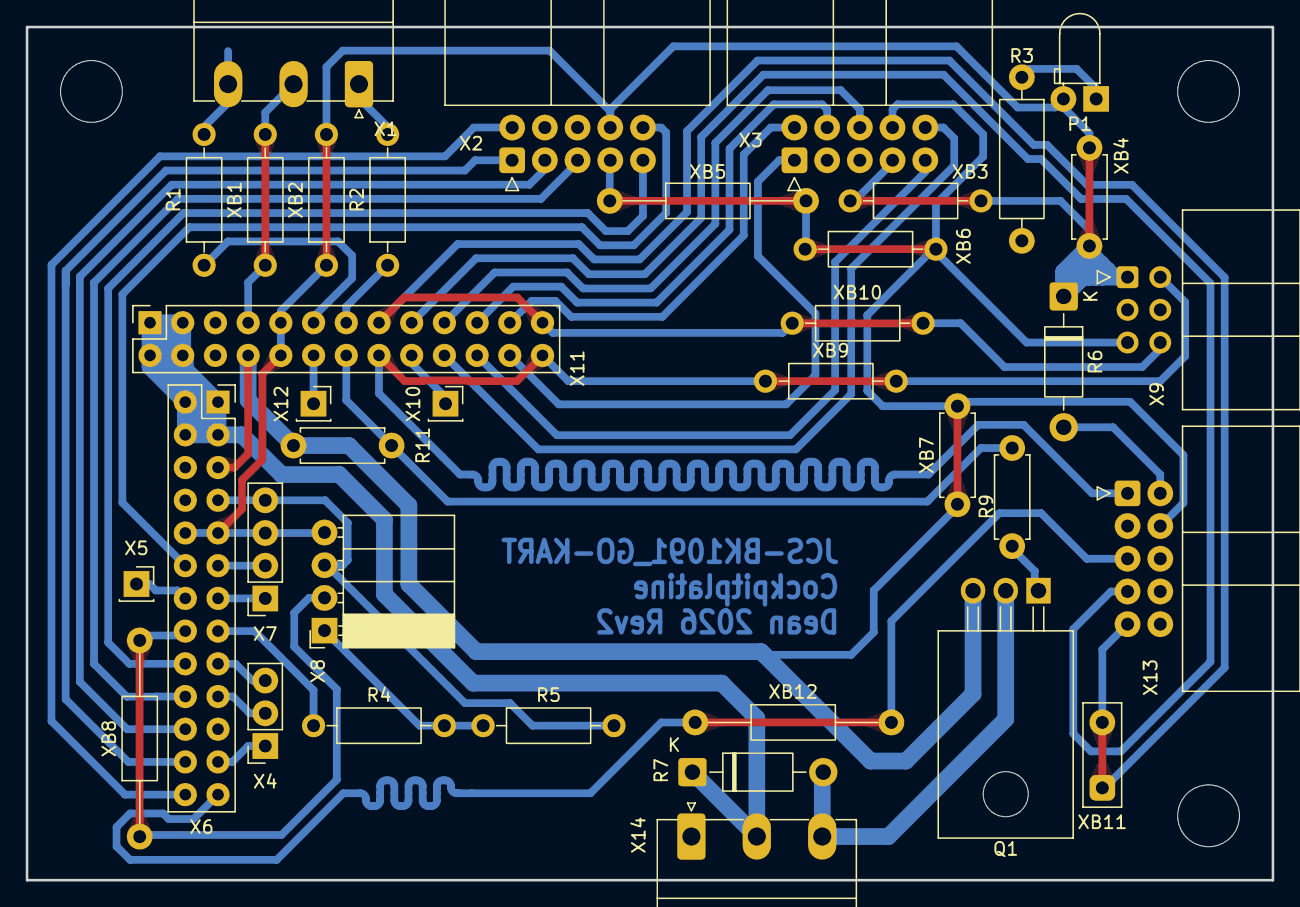
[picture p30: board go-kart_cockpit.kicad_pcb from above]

Board: 2 copper layers, 96.8 x 66.2 mm, 37 parts (0 on the bottom side), 39 nets.

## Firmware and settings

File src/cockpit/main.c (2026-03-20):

/*
 * Pinbelegung ist in hal.h zu finden.
 * uart0 für Steuerung des Displays.
 * uart1 für Ausgabe über Bluetooth.
 *
 * Author: Dean Schneider (GYT26)
 */

#include "can.h"
#include "cockpit_display.c"
#include "cockpit_display.h"
#include "hal.h"
#include "usart.h"
#include <avr/interrupt.h>
#include <avr/io.h>
#include <avr/iocan32.h>
#include <stdint.h>
#include <util/delay.h>

#define LOWER_LIGHT_BIT 0
#define BLINKER_BIT 1
#define UPPER_WEAK_LIGHT_BIT 2
#define UPPER_FULL_LIGHT_BIT 3

typedef enum {
  STOP,
  FORWARD,
  REVERSE,
} MotorState;

static const uint32_t CAN_ID_RX_BLINKER_STATE = 0x703;
static const uint32_t CAN_ID_RX_SPEED = 0x605;
static const uint32_t CAN_ID_RX_GEAR = 0x401;
static const uint32_t CAN_ID_RX_BATTERY = 0x302;
static const uint32_t CAN_ID_RX_POWER = 0x301;
static const uint32_t CAN_ID_RX_BRAKE = 0x201;

static const uint32_t CAN_ID_TX_BLINKER_FRONT_RIGHT = 0x604;
static const uint32_t CAN_ID_TX_BLINKER_FRONT_LEFT = 0x603;
static const uint32_t CAN_ID_TX_BLINKER_BACK_RIGHT = 0x602;
static const uint32_t CAN_ID_TX_BLINKER_BACK_LEFT = 0x601;
static const uint32_t CAN_ID_TX_DRIVE_STATE = 0x101;

MotorState motor_state = STOP;
GearState gear_state = GEAR_NEUTRAL;
LightState light_state = LIGHT_OFF;
bool warnblinker = false;
bool horn = false;
bool blinker_right = false;
bool blinker_left = false;

volatile bool blinker_left_live = false;
volatile bool light_switch = false;
volatile bool gear_up = false;
volatile bool gear_down = false;
volatile bool blinker_right_live = false;

#define TIMER0_SOFT_DIVISION 6
ISR(TIMER0_COMP_vect) {
  static uint8_t interrupt_count = 0;

  if (interrupt_count < TIMER0_SOFT_DIVISION) {
    interrupt_count++;
    return;
  }
  interrupt_count = 0;

  static bool previous_blinker_left = false;
  static bool previous_light_switch = false;
  static bool previous_gear_up = false;
  static bool previous_gear_down = false;
  static bool previous_blinker_right = false;

  // --- Einlesen ---
  const bool current_blinker_left = GET(SW_BLINKER_LEFT);
  const bool current_light_switch = GET(SW_LIGHT_SWITCH);
  const bool current_gear_up = GET(SW_GEAR_UP);
  const bool current_gear_down = GET(SW_GEAR_DOWN);
  const bool current_blinker_right = GET(SW_BLINKER_RIGHT);

  // --- Verarbeiten ---
  if (current_blinker_left && !previous_blinker_left) {
    // button pressed
    previous_blinker_left = true;
    blinker_left_live = !blinker_left_live;
  } else if (!current_blinker_left && previous_blinker_left) {
    // button released
    previous_blinker_left = false;
  } // current == previous -> nothing has changed

  if (current_light_switch && !previous_light_switch) {
    // button pressed
    previous_light_switch = true;
    SET(LED_LIGHT_SWITCH);
  } else if (!current_light_switch && previous_light_switch) {
    // button released
    previous_light_switch = false;
    RESET(LED_LIGHT_SWITCH);
    light_switch = true; // is set to false when processed
  } // current == previous -> nothing has changed

  if (current_gear_up && !previous_gear_up) {
    // button pressed
    previous_gear_up = true;
    SET(LED_GEAR_UP);
  } else if (!current_gear_up && previous_gear_up) {
    // button released
    previous_gear_up = false;
    RESET(LED_GEAR_UP);
    gear_up = true; // is set to false when processed
  } // current == previous -> nothing has changed

  if (current_gear_down && !previous_gear_down) {
    // button pressed
    previous_gear_down = true;
    SET(LED_GEAR_DOWN);
  } else if (!current_gear_down && previous_gear_down) {
    // button released
    previous_gear_down = false;
    RESET(LED_GEAR_DOWN);
    gear_down = true; // is set to false when processed
  } // current == previous -> nothing has changed

  if (current_blinker_right && !previous_blinker_right) {
    // button pressed
    previous_blinker_left = true;
    blinker_right_live = !blinker_right_live;
  } else if (!current_blinker_right && previous_blinker_right) {
    // button released
    previous_blinker_right = false;
  } // current == previous -> nothing has changed
}

void init(void) {
  uart0_init(BAUD_CALC(9600UL));
  uart1_init(BAUD_CALC(9600UL));
  hal_init();

  uart1_puts("\ninfo: JCS-BK_1091_GO-KART von Dean Schneider (GYT26)\n");
  uart1_puts("info: Cockpit Modul\n");

  if (!can_init(BITRATE_125_KBPS)) {
    while (true) {
      uart1_puts("fatal error: while can initialization\n");
      _delay_ms(1000);
    }
  }

  can_filter_t can_filter = {
      .id = 0,
      .mask = 0,             // disable ID filter, receive all
      .flags.extended = 0x3, // receive with extended id
      .flags.rtr = 0,        // only receive normal messaages (no RTR)
  };

  if (!can_set_filter(0, &can_filter)) {
    while (true) {
      uart1_puts("fatal error: while setting can message filters\n");
      _delay_ms(1000);
    }
  }

  // # configure timer for toggle buttons
  // clear timer value on compare match
  // and set prescaler to 1024: 16 MHz / 1024 = 15625 Hz
  TCCR0A = 1 << WGM01 | 1 << CS02 | 1 << CS00;
  // enable interrupt on compare match with OCR0A
  TIMSK0 = 1 << OCIE0A;
  // 15625 Hz / 255 = 61.27 Hz
  OCR0A = 255;
  // with a software division of 4: Timer0 at 15.32 Hz

  // these have default values at this point
  cd_set_gear(gear_state);
  cd_set_light(light_state);
}

typedef enum {
  LEFT,
  RIGHT,
} side_t;

/// @param send_to_right_side: true=right, false=left
void send_command_to_blinker_side(side_t to_right_side) {
  can_t msg_blinker = {
      .flags.rtr = false,
      .flags.extended = true,
      .length = 1,
  };

  uint8_t blinker_front_command = 0;
  uint8_t blinker_back_command = 0;

  if (to_right_side == RIGHT) {
    blinker_front_command |= blinker_right << BLINKER_BIT;
  } else if (to_right_side == LEFT) {
    blinker_front_command |= blinker_left << BLINKER_BIT;
  }

  switch (light_state) {
  case LIGHT_OFF:
    break;
  case LIGHT_DAY:
    blinker_front_command |= 1 << LOWER_LIGHT_BIT;
    break;
  case LIGHT_LOW_BEAM:
    blinker_front_command |= 1 << UPPER_WEAK_LIGHT_BIT | 1 << LOWER_LIGHT_BIT;
    break;
  case LIGHT_HIGH_BEAM:
    blinker_front_command |= 1 << UPPER_FULL_LIGHT_BIT | 1 << LOWER_LIGHT_BIT;
    break;
  case LIGHT_STATE_COUNT:
    break; // unreachable
  }

  if (to_right_side == RIGHT) {
    blinker_back_command |= blinker_right << BLINKER_BIT;
  } else if (to_right_side == LEFT) {
    blinker_back_command |= blinker_left << BLINKER_BIT;
  }

  if (light_state == LIGHT_LOW_BEAM || light_state == LIGHT_HIGH_BEAM) {
    blinker_back_command |= 1 << UPPER_WEAK_LIGHT_BIT;
  }

  uart1_puts("info: sende Befehl an Blinker vorne und hinten ");

  if (to_right_side == RIGHT) {
    uart1_puts("rechts");
  } else if (to_right_side == LEFT) {
    uart1_puts("links");
  }

  uart1_puts("\ninfo: Befehl vorne: 0x");
  uart1_puthex(blinker_front_command);
  uart1_puts("\ninfo: Befehl hinten: 0x");
  uart1_puthex(blinker_back_command);
  uart1_putc('\n');

  if (to_right_side == RIGHT) {
    msg_blinker.id = CAN_ID_TX_BLINKER_FRONT_RIGHT;
  } else if (to_right_side == LEFT) {
    msg_blinker.id = CAN_ID_TX_BLINKER_FRONT_LEFT;
  }
  msg_blinker.data[0] = blinker_front_command;
  can_send_message(&msg_blinker);

  if (to_right_side == RIGHT) {
    msg_blinker.id = CAN_ID_TX_BLINKER_BACK_RIGHT;
  } else if (to_right_side == LEFT) {
    msg_blinker.id = CAN_ID_TX_BLINKER_BACK_LEFT;
  }
  msg_blinker.data[0] = blinker_back_command;
  can_send_message(&msg_blinker);
}

void test_display(void);

int main(void) {
  init();
  sei();

  // test_display();

  GearState prev_gear_state = gear_state;
  LightState prev_light_state = light_state;
  bool prev_blinker_left = false;
  bool prev_horn = false;
  bool prev_blinker_right = false;
  bool prev_warnblinker = false;

  while (true) {
    // --- Einlesen ---
    blinker_left = blinker_left_live;
    blinker_right = blinker_right_live;
    horn = GET(SW_WARNBLINKER_HORN);

    if (GET(SW_MOTOR_START_LA)) {
      if (GET(SW_MOTOR_REVERSE_LA)) {
        motor_state = STOP;
      } else {
        motor_state = REVERSE;
      }
    } else {
      if (GET(SW_MOTOR_REVERSE_LA)) {
        motor_state = FORWARD;
      } else {
        motor_state = STOP;
        uart1_puts(
            "error: Vorwärts- und Rückwärtsfahren nicht gleichzeitig möglich."
            " Taster auf defekt überprüfen.\n");
      }
    }

    // --- Verarbeiten ---
    if (light_switch) {
      light_switch = false;
      light_state = (light_state + 1) % LIGHT_STATE_COUNT;
    }

    if (blinker_left && blinker_right) {
      warnblinker = true;
    } else if (warnblinker) {
      warnblinker = false;
    }

    if (gear_up) {
      gear_up = false;

      if (gear_state < GEAR_STATE_COUNT - 1) {
        gear_state++;
      }
    } else if (gear_down) {
      gear_down = false;

      if (gear_state > 0) {
        gear_state--;
      }
    }

    // --- Ausgeben ---
    if (light_state != prev_light_state) {
      cd_set_light(light_state);
    }

    if (horn != prev_horn) {
      if (horn) {
        SET(LED_WARNBLINKER_HORN);
        SET(HORN_PWM);
      } else {
        RESET(LED_WARNBLINKER_HORN);
        RESET(HORN_PWM);
      }
    }

    if (gear_state != prev_gear_state) {
      cd_set_gear(gear_state);
    }

    // some button LEDs are set in the ISR for simplicity

    if (warnblinker != prev_warnblinker) {
      if (warnblinker) {
        // reset blinker to synchronise them
        blinker_right = false;
        blinker_left = false;
        send_command_to_blinker_side(RIGHT);
        send_command_to_blinker_side(LEFT);

        // set blinker again
        blinker_right = true;
        blinker_left = true;
        prev_blinker_right = false;
        prev_blinker_left = false;
      } else {
        // disable both if one is disabled
        blinker_right = false;
        blinker_left = false;
        blinker_right_live = false;
        blinker_left_live = false;
      }
    }

    if (light_state != prev_light_state ||
        blinker_right != prev_blinker_right) {
      send_command_to_blinker_side(RIGHT);
    }

    if (light_state != prev_light_state || blinker_left != prev_blinker_left) {
      send_command_to_blinker_side(LEFT);
    }

    if (blinker_left != prev_blinker_left) {
      cd_set_blinker_left(blinker_left);

      if (blinker_left) {
        SET(LED_BLINKER_LEFT);
      } else {
        RESET(LED_BLINKER_LEFT);
      }
    }

    if (blinker_right != prev_blinker_right) {
      cd_set_blinker_right(blinker_right);

      if (blinker_right) {
        SET(LED_BLINKER_RIGHT);
      } else {
        RESET(LED_BLINKER_RIGHT);
      }
    }

    prev_blinker_left = blinker_left;
    prev_gear_state = gear_state;
    prev_light_state = light_state;
    prev_horn = horn;
    prev_blinker_right = blinker_right;
    prev_warnblinker = warnblinker;
  }

emergency_loop:
  goto emergency_loop;
}

void test_display(void) {
  cd_set_rpm(789);
  cd_set_speed(12);

  cd_set_throttle(80);
  cd_set_brake(60);

  while (true) {
    cd_set_blinker_left(true);
    _delay_ms(200);
    cd_set_blinker_left(false);
    _delay_ms(200);

    cd_set_blinker_right(true);
    _delay_ms(200);
    cd_set_blinker_right(false);
    _delay_ms(200);

    cd_set_warnblinker(true);
    _delay_ms(500);
    cd_set_warnblinker(false);
    _delay_ms(500);

    cd_set_light(LIGHT_DAY);
    _delay_ms(700);
    cd_set_light(LIGHT_LOW_BEAM);
    _delay_ms(700);
    cd_set_light(LIGHT_HIGH_BEAM);
    _delay_ms(700);

    cd_set_gear(GEAR_NEUTRAL);
    _delay_ms(200);
    cd_set_gear(GEAR_FIRST);
    _delay_ms(200);
    cd_set_gear(GEAR_SECOND);
    _delay_ms(200);
    cd_set_gear(GEAR_THIRD);
    _delay_ms(200);

    cd_set_battery(BATTERY_EMPTY);
    _delay_ms(500);
    cd_set_battery(BATTERY_ONE_FOURTH);
    _delay_ms(500);
    cd_set_battery(BATTERY_TWO_FOURTH);
    _delay_ms(500);
    cd_set_battery(BATTERY_THREE_FOURTH);
    _delay_ms(500);
    cd_set_battery(BATTERY_FOUR_FOURTH);
    _delay_ms(500);
    cd_set_battery(BATTERY_CHARGING);
    _delay_ms(500);

    _delay_ms(2000);
  }
}

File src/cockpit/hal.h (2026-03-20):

/*
 * HAL (Hardware Abstraction Layer) ist eine Programmierschicht,
 * die die Hardware eines Mikrocontrollers durch einfache,
 * einheitliche Funktionen abstrahiert.
 * Dadurch wird der Code leichter lesbar, wartbarer und besser portierbar.
 * Allerdings oft etwas langsamer und größer als reiner Low-Level-Code.
 *
 * Author: Dean Schneider (GYT26)
 */

#ifndef HAL_H
#define HAL_H

#include <avr/io.h>

// Beispiel: PORTC PC6 => C, 6

// --- PORTB ---
#define ISP_SCK B, 1
#define ISP_MOSI B, 2
#define ISP_MISO B, 3
#define HORN_PWM B, 4
/// LA = low active
#define SW_MOTOR_START_LA B, 5
#define SW_MOTOR_REVERSE_LA B, 7

// --- PORTC ---
#define SW_BLINKER_RIGHT C, 0
#define LED_BLINKER_RIGHT C, 3

// --- PORTD ---
#define UART1_RX D, 2
#define UART1_TX D, 3
#define LED_GEAR_UP D, 4

// --- PORTE ---
#define UART0_RX_DISPLAY E, 0
#define UART0_TX_DISPLAY E, 1
#define LED_BLINKER_LEFT E, 2
#define SW_BLINKER_LEFT E, 3
#define LED_LIGHT_SWITCH E, 4
#define SW_LIGHT_SWITCH E, 5
#define LED_WARNBLINKER_HORN E, 6
#define SW_WARNBLINKER_HORN E, 7

// --- PORTG ---
#define SW_GEAR_UP G, 0
#define SW_GEAR_DOWN G, 2
#define LED_GEAR_DOWN G, 3

#define _SET2(port, bit) PORT##port |= (1 << bit)
#define _GET2(port, bit) ((PIN##port >> bit) & 1)
#define _RESET2(port, bit) PORT##port &= ~(1 << bit)
#define _TOGGLE2(port, bit) PORT##port ^= (1 << bit)
#define _SET_INPUT2(port, bit) DDR##port |= (1 << bit)
#define _SET_OUTPUT2(port, bit) DDR##port |= (1 << bit)

// Beispiel: SET(LED_BLINKER_0);
// => _SET2(D, 5);
// => PORTD |= (1 << 5);

#define SET(port_comma_bit) _SET2(port_comma_bit)
#define GET(port_comma_bit) _GET2(port_comma_bit)
#define RESET(port_comma_bit) _RESET2(port_comma_bit)
#define TOGGLE(port_comma_bit) _TOGGLE2(port_comma_bit)
#define SET_INPUT(port_comma_bit) _SET_INPUT2(port_comma_bit)
#define SET_OUTPUT(port_comma_bit) _SET_OUTPUT2(port_comma_bit)

#define _P2(port, bit) (1 << bit)
#define _P(port_comma_bit) _P2(port_comma_bit)

void hal_init(void) {
  // enable pull up resistors
  SET(SW_MOTOR_START_LA);
  SET(SW_MOTOR_REVERSE_LA);

  // set output pins
  DDRB = _P(HORN_PWM);
  DDRC = _P(LED_BLINKER_RIGHT);
  DDRD = _P(UART1_TX) | _P(LED_GEAR_UP);
  DDRE = _P(UART0_TX_DISPLAY) | _P(LED_BLINKER_LEFT) | _P(LED_LIGHT_SWITCH) |
         _P(LED_WARNBLINKER_HORN);
  DDRG = _P(LED_GEAR_DOWN);
}

#endif

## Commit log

2025-09-12 feat(pflichtenheft): add first page and rough layout
    [machbarkeitsanalyse.ods, tagesziele.ods, terminplan.ods]
2025-09-22 feat: insert lastenheft into pflichtenheft
2025-09-22 feat: add projects of predecessors, add goals and existing things
    [_summary.ods]
2025-09-25 feat(pflichtenheft): Terminplan eingefügt
    [machbarkeitsanalyse.ods, tagesziele.ods, terminplan.ods]
2025-09-26 feat(pflichtenheft): change structure and insert missing tables
    [_summary.ods, alte_projekte.ods, machbarkeitsanalyse.ods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]
2025-09-26 feat(pflichtenheft): insert title image
    [alte_projekte.ods]
2025-09-27 feat: Aufgabenstellung und alte Projekte
    [tagesziele.ods]
2025-09-28 docs(Plichtenheft): erste Abgabe ohne Überarbeitung
    [tagesziele.ods, terminplan.ods]
2025-10-08 feat: Pflichtenheft Korrektur
    [alte_projekte.ods, tagesziele.ods, terminplan.ods]
2025-11-30 feat: final touches on documentation for draft 1
    [tagesziele.ods, terminplan.ods]
2026-01-20 docs: Schaltplan für Bluetooth, cmake Erklärung, CAN-Sniffing
    [alte_projekte.ods, circuit.kicad_pcb, circuit.kicad_sch]
2026-01-22 docs: sort alte projekte in descending order
    [alte_projekte.ods]
2026-01-23 docs: draft 2 documentation, add Tagesziele
    [tagesziele.ods, terminplan.ods]
2026-01-24 feat: test LEDs of blinker module
2026-01-24 WIP(blinker): set up can bus
2026-01-28 fix: usart library for AT90CAN32
    [main.c]
2026-01-28 feat: test cockpit display with AT90CAN32, fix cockpit display library
    [main.c]
2026-01-30 feat: successful CAN-Bus test with AT90CAN
2026-02-01 feat: successful CAN-Bus echo test with ATmega16M1
2026-02-04 feat: (untested) add commands, add UART for ATmega16M1
2026-02-09 style: reformat uart_AM16M1.h
2026-02-09 feat: control blinker with UART (with bug)
    [main.c]
2026-02-09 feat: PWM for break and backlight, send periodically state over CAN
2026-02-10 fix: PWM was not fast enough, Blinker-Modul is working
    [main.c]
2026-02-10 docs: create CAN ID table
    [can_ids.ods]
2026-02-11 fix: do not send light state if UART command failed
    [main.c]
2026-02-11 feat: CAN_ID table first version
    [can_ids.ods]
2026-02-12 feat(blinker): use correct CAN IDs and state message
    [main.c]
2026-02-12 fix(blinker): lower light is turned off by blinker code
    [can_ids.ods]
2026-02-12 feat: circuit for switches
    [circuit.kicad_pcb, circuit.kicad_sch, go-kart_cockpit.kicad_sch]
2026-02-12 WIP: planning cockpit pins
    [go-kart_cockpit.kicad_sch]
2026-02-12 WIP: circuit
    [go-kart_cockpit.kicad_pcb, go-kart_cockpit.kicad_sch]
2026-02-12 feat(circuit): use internal pull up resistors
    [go-kart_cockpit.kicad_sch]
2026-02-13 feat: circuit before rework with larger plate
    [go-kart_cockpit.kicad_pcb, go-kart_cockpit.kicad_sch]
2026-02-15 feat: planned connections to MCU
    [go-kart_cockpit.kicad_pcb, go-kart_cockpit.kicad_sch]
2026-02-15 feat: set pins in code
    [can_ids.ods, go-kart_cockpit.kicad_sch]
2026-02-15 feat: cockpit test code (untested)
    [can_ids.ods]
2026-02-15 feat: TI_Zwischenabgabe
    [can_ids.ods]
2026-02-16 feat: first sketch of PCB
    [go-kart_cockpit.kicad_pcb, go-kart_cockpit.kicad_sch]
2026-02-16 feat(circuit): fixed DRC
    [go-kart_cockpit.kicad_pcb, go-kart_cockpit.kicad_sch]
2026-02-16 feat(circuit): final touches
    [go-kart_cockpit.kicad_pcb, go-kart_cockpit.kicad_sch]
2026-02-16 feat(PCB): checklist and LED calculation
    [go-kart_cockpit.kicad_pcb, go-kart_cockpit.kicad_sch]
2026-02-16 feat(PCB): add pull down resistor in preperation for FET
    [go-kart_cockpit.kicad_pcb, go-kart_cockpit.kicad_sch]
2026-02-16 feat(PCB): add teardrops
    [go-kart_cockpit.kicad_pcb]
2026-02-17 feat(PCB): improve connectors and position
    [go-kart_cockpit.kicad_pcb, go-kart_cockpit.kicad_sch]
2026-02-17 feat(PCB): replace TIP120 with MOSFET
    [go-kart_cockpit.kicad_pcb, go-kart_cockpit.kicad_sch]
2026-02-20 feat: cleanup Tasterinnenbeschaltung for presentation
    [go-kart_cockpit.kicad_sch]
2026-03-02 feat: rework of PCB, fix wrong connection
    [go-kart_cockpit.kicad_pcb, go-kart_cockpit.kicad_sch]
2026-03-03 feat(PCB): replace 100 ohm preresistors with 330
    [go-kart_cockpit.kicad_pcb, go-kart_cockpit.kicad_sch]
2026-03-03 fix(PCB): green connector drill holes are too small, built PCB
    [go-kart_cockpit.kicad_pcb]
2026-03-03 feat(cockpit): update hal to reflect PCB change
2026-03-04 WIP(cockpit): test PCB
2026-03-05 feat(cockpit): test all switches
2026-03-05 feat(cockpit): read switches with interrupt
2026-03-05 feat(cockpit): toggleable buttons
2026-03-05 feat(cockpit): control blinker with can bus (untested)
2026-03-06 fix(PCB): ISP is actually connected to UART0 instead of SPI
    [go-kart_cockpit.kicad_pcb, go-kart_cockpit.kicad_sch]
2026-03-07 docs: rename can_ids to can_protokoll
    [can_protokoll.ods]
2026-03-07 docs: inserted PCB graphics, general improvements
2026-03-07 docs: add communication diagram, add finished products
    [can_protokoll.ods]
2026-03-07 feat(blinker): use more accurate timer values
2026-03-08 docs: add communication diagram
    [can_protokoll.ods]
2026-03-12 feat: update program for blinkers
    [can_protokoll.ods]
2026-03-13 docs: update Terminplan
    [tagesziele.ods, terminplan.ods]
2026-03-17 fix(cockpit): bug with setting blinker, improve debug messages
    [main.c]
2026-03-19 refactor(blinker): rename uart library
2026-03-20 fix(cockpit): turning off warnblinker does not deactivate light, more time between button reading
    [main.c]
2026-03-22 fix(blinker): add volatile to variables which are modified by interrupt
    [main.c]
2026-03-22 feat(blinker): UART with buffer (interrupt)
